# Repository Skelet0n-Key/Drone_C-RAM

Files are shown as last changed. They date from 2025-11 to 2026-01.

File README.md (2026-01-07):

# Project Overview

**Introduction**

Inspired by C-RAM/CIWS systems, an embedded systems semester-long team project was built. This ML vision air defense turret prototype is intended to combat small drones at close range, as a last line of defense. The system features dual TB6600s driving yaw and pitch stepper motors to their thermal limits. 3D printed and belt drive hardware allows for independent gear reduction for each axis. A Raspberry Pi 5 with locally running ML image recognition (YOLOv8) handles detection and sends coordinates on the screen to an Arduino via UART. The Arduino calculates the x and y stepper motor movement, using timers to send the correct frequency and steps to lock onto targets. The use of Raspberry Pi (Linux) and Arduino (bare metal C++) allows for ease of use, flexible programming, and direct real time control. The turret design accepts any AR style air-soft gun via piccatinny rail.

<p align="center">
  <a href="https://youtu.be/CiCFE5r0B4Y" target="_blank">
    YouTube Video Thumbnail
  </a>
  <br>
  <a href="https://youtu.be/CiCFE5r0B4Y" target="_blank">
    Watch demo video on YouTube
  </a>
  <br><br>
  <a href="https://www.youtube.com/playlist?list=PLNzJUv3sgPipa0nPbpG0y632YNqH1CYb0" target="_blank">
    View the full playlist here
  </a>
</p>

**Project Capabilities**

- Powered via standard 120V corded 24V power supply or 18-24V drill batteries. System intended to run on 24V DC.
- X stepper motor wires and main power runs through a 6 wire gold plated slip joint in the base of the turret, allowing for unrestricted 360 degree rotation.
- The sony IMX500 ASIC can be loaded with various tensorflow and yolo image recognition models. Read more here: [(+)](https://www.raspberrypi.com/documentation/accessories/ai-camera.html)
- The turret can be set to detect, track, and fire on drones or people. Target prediction is an option for both person and drone modes. 
- Can be configured to automatically run when plugged in. 
- Effective range: 20-30 feet.
- Theoretical max turret rotation: 150 rpm. Realistically, rotation speed is limited by when motion blur in the camera prevents ML from detecting targets, or when target leaves the frame too quickly for the turret to accelerate.  

**Timeline**

- Working model with object detection (10/14/25)
- Finished printing and received all parts to build the project (10/20/25)
- Project assembled (10/22/25)
- Motor control working (10/29/25)
- PID controller implemented, motor control refined (11/2/25)
- Turret locking on people (11/5/25)
- AI trained on drones (12/4/25)
- First field tests (12/6/25)

**Testing and Results**
- Ssd_mobilenet_v2 general ML model delivering exceptional results when filtered to detect people only.
- Custom yolov8 model trained on generic publc dataset delivering mediocre results. Detection spotty, drops frames, slow. Better dataset needed.
- Turret holds acceptable accuracy and is fast with good ML model
- Hard stop switches too sensitive, vibration from firing causes them to trip, recalibrating turret mid firing.
- Initial field test, 2 confirmed hits on drone.
- Second tests, C-RAM tracking incredibly well running around it ~25ft away. Discovered that it will lock onto people's shadows if the silhouette is human enough.

# Challenges & Solutions

**Learning to interface with the raspberry pi AI cam with integrated IMX500 ASIC to run ML locally**

The Libcamera library for the pi AI cam has been renamed rpicam, Libcamera is no longer in use. Our python script utilizes picamera2 to run a mobilenetSSD model, and cv2 to draw center mass points for output bounding boxes.

**Developing a robust driver for dual TB6600s and NEMA 17 stepper motors**

Finding max PUL speeds for our motors to avoid overloading and skipping. Finding min PUL pulse timing for smooth motion with reasonable micro-stepping. Finding optimal torque curves to avoid belt skipping and jitter. Method for finding these limits was trial and error, changing pusle speed in software and testing movements for hours. We settled on driving the TB6600s with arduino to supply the required 5v input signals and avoid Linux operating system real time control issues. By offloading stepper control to a bare metal micro controller we achieved smooth and precise control.

**Designing a printable frame, utilizing common and widely available hardware. (shafts, bearings, belts, etc...)**

We chose to use standard 3d printer parts for most of the hardware on the frame for accessibility and standardization. There are a couple random odds and ends like a 4" turntable bearing and a 6 wire gold contact slip joint for 360 degree rotation.

**Accurately calculating target lead**

The target lead is based off of the target's speed across the feed. This creates problems when the camera is on the turret, which is rotating. A target may be stationary, but the movement of the camera will cause it to think that the target is moving. It will calculate a lead and oscillate over the stationary target. We considered mounting the camera on the baseplate rather than move with the turret, but this creates more problems than it solves. The turret doesn't know its exact orientation, and a setup like this would need to. The mounted camera also allows for this feedback loop. Were it on the baseplate, the turret would constantly get misaligned and miss its target. Our best solution was to dampen the sent coordinates. This minimized oscillation and conveniently also helped the target leading algorithm to be more smooth.

**Implementing PID controller in C++ for smooth turret rotation**

The actual controller implementation is more of a PD controller. That is - the turret is rotated on its proportional and derivative components, or how far away the target is relative to center, and how fast the turret is approaching its target.

**Using a MOSFET to pull the trigger**

We thought that it would be nice to digitally pull the trigger. A MOSFET was the perfect addition. We ended up going with the N-channel IRLB8721 MOSFETs. After wiring it all up to the battery at drove the firing mechanism, the MOSFET started to smoke and melt the jumper wires. The battery GND and Arduino GND were connected, the specifications for the transistor weren't being exceeded... Due to an impending project deadline, we attached another stepper motor to the turret to pull the trigger. This comes with its own issues. We couldn't pull the power if the trigger was still held down, the Arduino needed to tell it to back off. Silver lining though, putting the battery on the outside of the stock balanced the turret a bit more.

**Turret pitching too violently on drone model**

Unfortunately, this was a result of an imperfect yolov8 model. Especially indoors, the model had a hard time keeping track of the drone. The turret updates its stepper-controlling timers everytime a coordinate is received from the RPI5. It has a timeout function to stop if it hasn't received a coordinate for a (long) time. Because the drone model was constantly timing out, it was over-rotating and then overcorrecting when it got a detection again. We patched this by lowering the timeout time. This actually made it timeout more, but stopped the turret from over-rotating. It makes the motion for drone tracking much more choppy. A permanent solution would be to get a more continuous output of coordinates with a better AI model, or to re-write the entire controller logic on the Arduino to handle less continuous coordinates better.

**Turret jerking on drone model**

This was an interesting issue. Prior to the updated stepper motor control code as it is now, the code used to have separated direction and speed control functions. This was an attempt to make portable, abstract, and modular code. What it ended up doing on less reliable models was jerking when switching directions. So if the drone was on the right side of the screen, it would accelerate right until the target moved, blinked and appeared on the left side of the screen. The speed controller was only aware of speed and distance to target, so the direction would switch instantaneously, while the frequency sent to the stepper motors stayed relatively the same. This wasn't an issue with a better model like tracking people. The detections didn't "blink" across the screen, there were continuous coordinates sent to the Arduino. The solution: unify the direction and frequency control functions. That way, if the turret is rotating clockwise but needs to rotate counter-clockwise, it decelerates to zero before switching directions.

**Turret re-calibrating when firing**

Earlier, we added buttons on the yolk that would be physically switched when the turret pitched too far up or down. The buttons would trigger an interrupt and the turret would "recover" or "re-calibrate." This recalibration was blocking, so perhaps it was for the best that we had issues here: for some reason, when the turret was firing this interrupt was triggering, despite neither button being pressed. We theorize that the vibration of the turret was somehow making the code go into that logic. Maybe the vibration was producing a signal on a victim line from some other aggressor line. We ended up doing away with the re-calibration logic.

# Hardware Components

* (5) 5mm x 250mm 304 Stainless Steel Solid Round Rod [(+)](https://www.amazon.com/dp/B082ZNJR7D?ref=ppx_yo2ov_dt_b_fed_asin_title&th=1)
* (12) Set Screw Collars [(+)](https://www.amazon.com/dp/B0F9P5CNSL?ref=ppx_yo2ov_dt_b_fed_asin_title&th=1)
* (15) Ball Bearings 5mm Bore 16mm OD [(+)](https://www.amazon.com/dp/B0CJFSBRTJ?ref=ppx_yo2ov_dt_b_fed_asin_title&th=1)
* (4) Flange Coupling Connector [(+)](https://www.amazon.com/dp/B0DN6P9B36?ref=ppx_yo2ov_dt_b_fed_asin_title&th=1)
* (2) Timing Pulley Set [(+)](https://www.amazon.com/dp/B09TKZS2QB?ref=ppx_yo2ov_dt_b_fed_asin_title&th=1)
* Turntable Bearing [(+)](https://www.amazon.com/dp/B08CSMYXFV?ref=ppx_yo2ov_dt_b_fed_asin_title&th=1)
* Raspberry Pi AI camera [(+)](https://www.adafruit.com/product/6009?srsltid=AfmBOoqx1-qlwzmA9ndyD2iXr5zASwpQUE9RnnWQQf-xEFGbjSt2rt4W)
* Stepper motor cables [(+)](https://www.amazon.com/dp/B07PZWXBFB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)
* Power supply [(+)](https://www.amazon.com/dp/B0CGHSTDYM?ref_=cm_sw_r_cp_ud_ct_X4HZC6Q636RNBEGBQEZB_1&th=1)
* Jumper cables [(+)](https://www.amazon.com/dp/B0CGHSTDYM?ref_=cm_sw_r_cp_ud_ct_X4HZC6Q636RNBEGBQEZB_1&th=1)
* Raspberry Pi 5 8GB [(+)](https://www.amazon.com/dp/B0CK2FCG1K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)
* (2) TB6600 stepper motor drivers [(+)](https://www.amazon.com/dp/B0BZYX7Z4Z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)
* Full automatic arisoft gun (some prints made specific to our model [(+)](https://www.amazon.com/dp/B07XJ9K5KT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))
* Slip joint [(+)](https://www.amazon.com/dp/B07XJ9K5KT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)
* Arduino Uno [(+)](https://www.amazon.com/Arduino-A000066-ARDUINO-UNO-R3/dp/B008GRTSV6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)
* 12V/24V to 5V Power Converter [(+)](https://www.amazon.com/dp/B0CJV6WV35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)

# Software Dependencies

Raspberry PI:

```bash
    sudo apt install imx500-all 
    sudo apt install python3-picamera2 --no-install-recommends
```

# Implementation

## Wiring Diagram
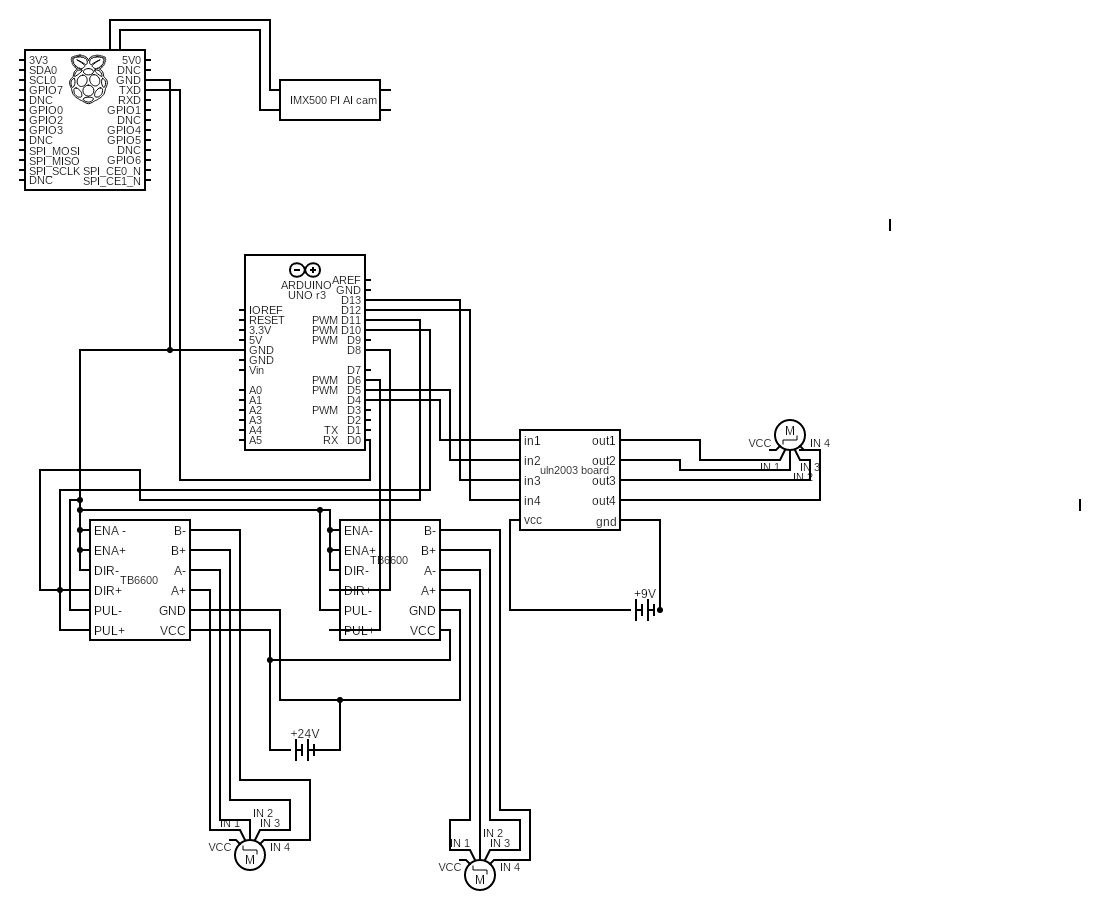
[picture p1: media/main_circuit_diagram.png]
wiring diagram


## CAD Files

We used a total of (seven) 3D printed parts on this project. You can find them here: [(+)](https://github.com/Skelet0n-Key/Drone_C-RAM/tree/main/CAD_files)

# Helpful Resources
- Raspberry PI AI Camera Guide [(+)](https://www.raspberrypi.com/documentation/accessories/ai-camera.html)
- Raspberry Pi AI Camera IMX500 Converter User Manual [(+)](https://developer.aitrios.sony-semicon.com/en/docs/raspberry-pi-ai-camera/imx500-converter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)
- Post-Training Quantization in PyTorch using the Model Compression Toolkit [(+)](https://github.com/SonySemiconductorSolutions/mct-model-optimization/blob/main/tutorials/notebooks/mct_features_notebooks/pytorch/example_pytorch_post_training_quant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)
- Export a Quantized Pytorch Model With the Model Compression Toolkit [(+)](https://github.com/SonySemiconductorSolutions/mct-model-optimization/blob/main/tutorials/notebooks/mct_features_notebooks/pytorch/example_pytorch_export.ipynb)
- MCT Features [(+)](https://github.com/SonySemiconductorSolutions/mct-model-optimization/tree/main/tutorials/notebooks/mct_features_notebooks)

# Acknowledgements
- We used an example from picamera2 [(+)](https://github.com/raspberrypi/picamera2/blob/3b2889e2c3eb1f05b5bb16d08be98b9f5355748f/examples/imx500/imx500_object_detection_demo.py) as the scaffolding for our ML_control [(+)](https://github.com/Skelet0n-Key/Drone_C-RAM/tree/main/ML_control) programs.

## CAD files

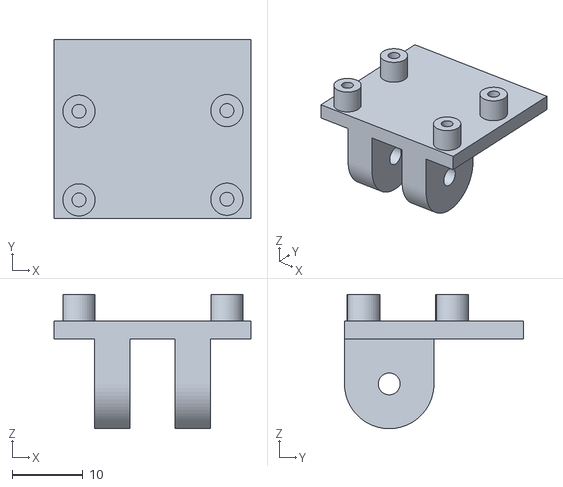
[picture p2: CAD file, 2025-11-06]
CAD_files/pi cam mount v2.stl
27.9 x 25.4 x 19.0

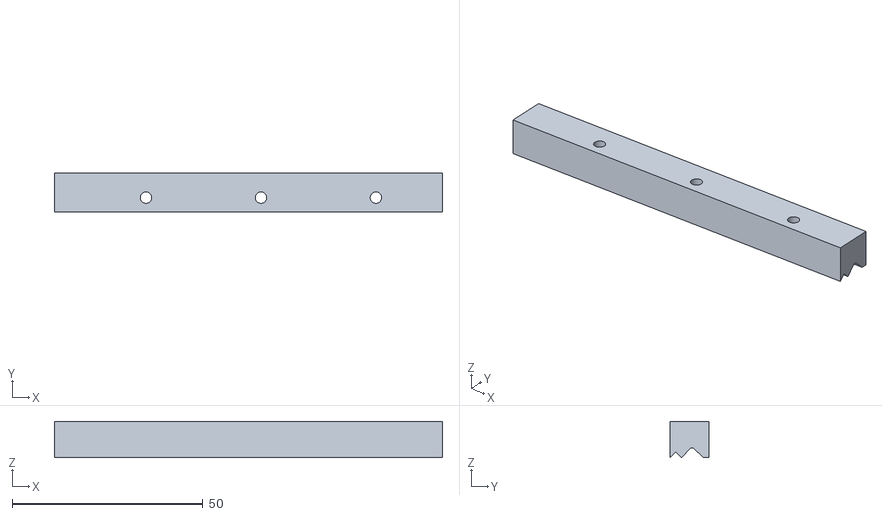
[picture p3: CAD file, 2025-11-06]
CAD_files/pic rail for gun mount v3.stl
101.6 x 10.2 x 9.48

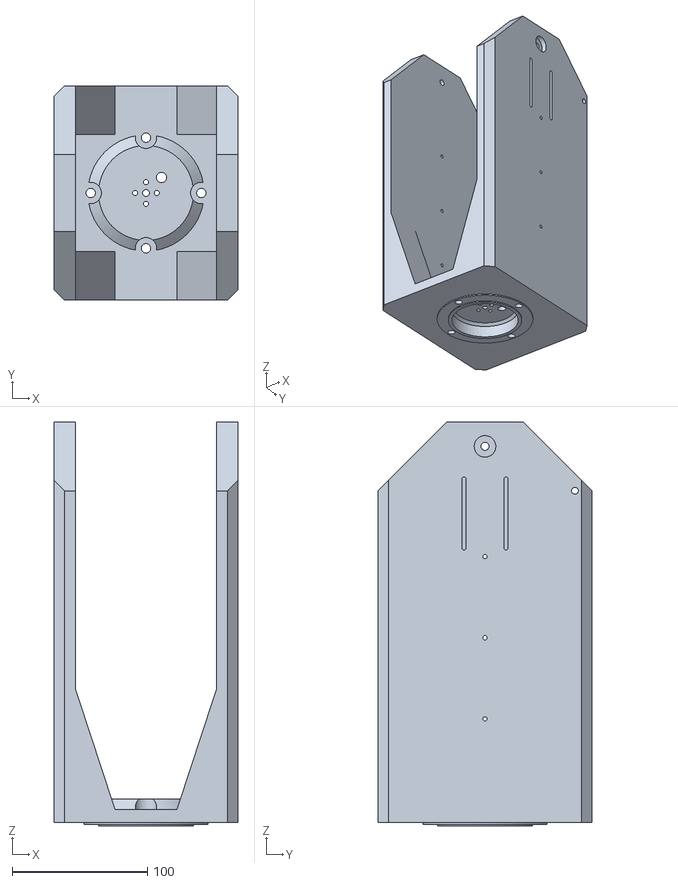
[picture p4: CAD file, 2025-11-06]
CAD_files/turret yoke v13.stl
135.9 x 158.1 x 298.5

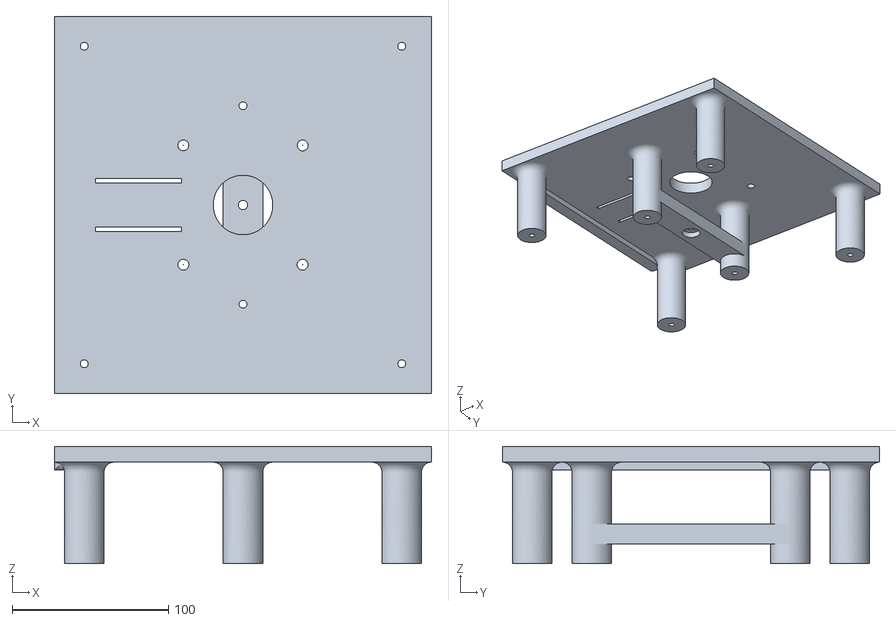
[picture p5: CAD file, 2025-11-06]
CAD_files/turret_baseplate_final v7.stl
241.3 x 241.3 x 75.2

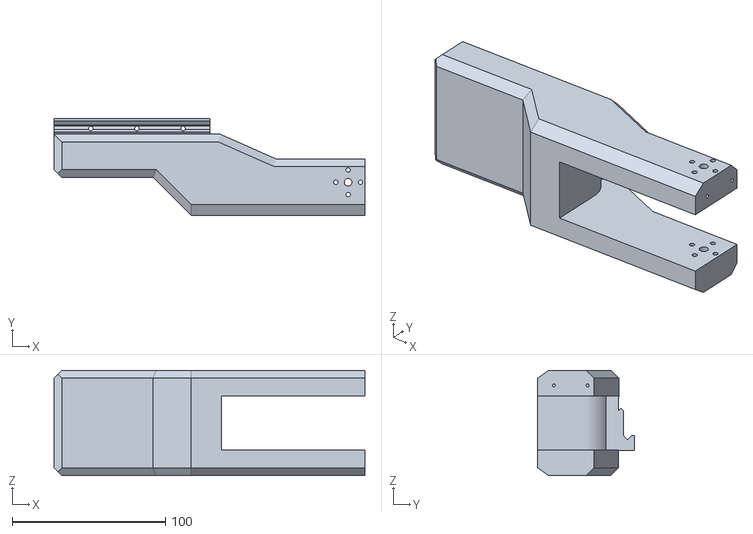
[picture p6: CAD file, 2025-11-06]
CAD_files/gun mount v7.stl
202.8 x 63.1 x 68.6

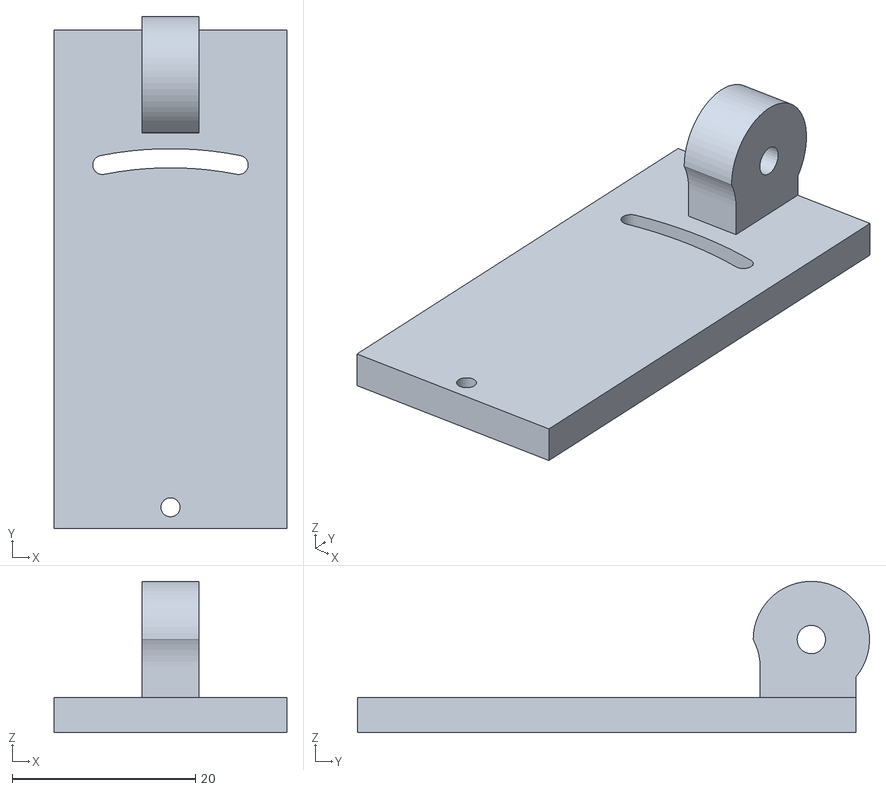
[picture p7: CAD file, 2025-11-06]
CAD_files/picam mount base v3.stl
25.4 x 55.9 x 16.5

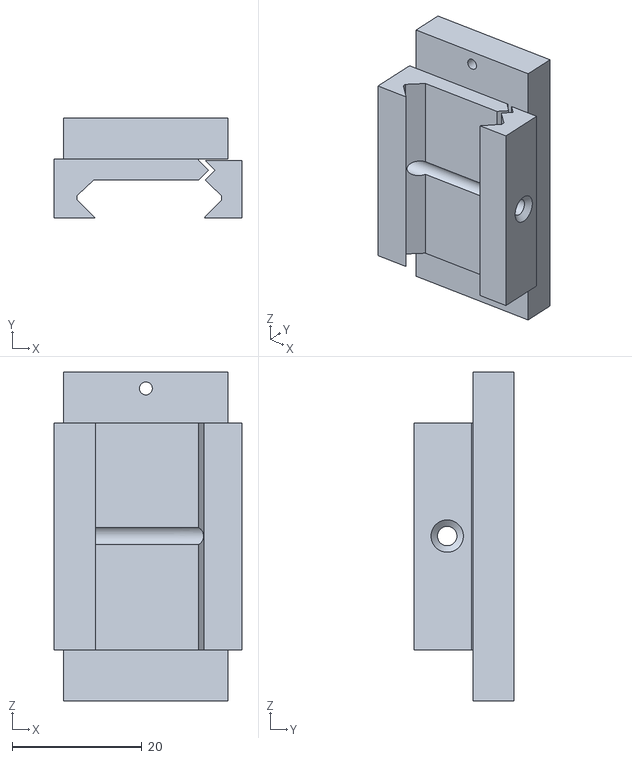
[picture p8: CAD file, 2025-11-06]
CAD_files/picamRailbase v3.stl
29.0 x 15.5 x 50.8

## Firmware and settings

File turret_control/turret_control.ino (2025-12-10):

/*
 Y tb6600 setting 4 microstep (on off off)
 X tb6600 setting 2b microstep(off on on)
 both amp setting 2.5 (off on on)
*/

#include <Arduino.h>

String coords = "";
int x = 0;
int y = 0;
int centerX = 320;
int centerY = 240;
int xFreq = 100;
int yFreq = 100;

int xPulsePin = 6;   // Timer0 OCR0A
int xDirPin = 8;
int yPulsePin = 11;  // Timer2 OCR2A
int yDirPin = 10;

// y-limit switches
const int Y_DOWN_LIMIT_PIN = 2;
const int Y_UP_LIMIT_PIN = 3;

volatile bool yLimitLock = false;
volatile bool yUpLimit = false;
volatile bool yDownLimit = false;
volatile bool yRecover = false;
volatile bool scan = false;

// ULN2003 stepper pins
const int STEP_IN1 = 4;
const int STEP_IN2 = 5;
const int STEP_IN3 = 12;
const int STEP_IN4 = 13;

int pinlist[] = {4, 5, 12, 13};

const int STEPS_PER_REV = 2048;
const int STEPS_PER_EIGHTH = STEPS_PER_REV / 2;

// Half-step sequence for trigger stepper
const int sequence[8][4] = {
  {1,0,0,0},
  {1,1,0,0},
  {0,1,0,0},
  {0,1,1,0},
  {0,0,1,0},
  {0,0,1,1},
  {0,0,0,1},
  {1,0,0,1}
};

// Stepper state
struct StepperState {
  int currentStep = 0;
  int stepsRemaining = 0;
  int direction = 1;
  unsigned long lastStepTime = 0;
  int stepDelay = 1; // ms
  bool active = false;
  bool stateFired = false; // has fire been triggered
} stepper;


// Timeout vars
volatile unsigned long timer1_millis = 0;
unsigned long millis_without_coords = 0;

// Turret behavior params
const double X_CURVE_COEFFICIENT = 2;
const int X_FREQ_MAX = 2000;
const int X_FREQ_MIN = 31;
const int X_ACCEL_LIMIT = 70;
const double Y_CURVE_COEFFICIENT = 4;
const int Y_FREQ_MAX = 2000;
const int Y_FREQ_MIN = 31;
const int Y_ACCEL_LIMIT = 50;

const int X_DEADZONE = 15;  // true deadzone is times two
const int Y_DEADZONE = 15;

const int X_FIRE_DEADZONE = 30;
const int Y_FIRE_DEADZONE = 30;

// Function prototypes for turret control
void stopTimer0();
void startTimer0();
void stopTimer2();
void startTimer2();
void setxFreq(int xFreq);
void setyFreq(int yFreq);
int xfrequency_calculator(int coord, int curr_freq, int center);
int yfrequency_calculator(int coord, int curr_freq, int center);
void set_dir(char axis, int center, int coord);

// Stepper functions
void updateStepper();
void driveStepper(bool fire);
void releaseCoils();

void setup() {
  // Timer0 - prescaler 1024, 1kHz output on Pin 6 (X-axis)
  TCCR0A = (1 << COM0A0) | (1 << WGM01);  // Toggle mode, CTC mode
  TCCR0B = (1 << CS02) | (1 << CS00);     // Prescaler 1024
  OCR0A = (uint8_t)((F_CPU / (2UL * 1024UL * 1000UL)) - 1);

  // Timer1 setup for 1ms interrupts
  TCCR1A = 0;  // Normal mode
  TCCR1B = (1 << WGM12) | (1 << CS11) | (1 << CS10);  // CTC mode, prescaler 64
  TCNT1 = 0;
  OCR1A = 249;  // 16MHz / 64 / 250 = 1000 Hz (1ms)
  TIMSK1 |= (1 << OCIE1A);  // Enable compare interrupt
  sei();  // Enable global interrupts
  
  // Timer2 - prescaler 1024, 1kHz output on Pin 11 (Y-axis)
  TCCR2A = (1 << COM2A0) | (1 << WGM21);  // Toggle mode, CTC mode
  TCCR2B = (1 << CS22) | (1 << CS21) | (1 << CS20);  // Prescaler 1024
  OCR2A = (uint8_t)((F_CPU / (2UL * 1024UL * 1000UL)) - 1);
  
  pinMode(xPulsePin, OUTPUT);
  pinMode(xDirPin, OUTPUT);
  pinMode(yPulsePin, OUTPUT);
  pinMode(yDirPin, OUTPUT);

  pinMode(4, OUTPUT);
  pinMode(5, OUTPUT);
  pinMode(12, OUTPUT);
  pinMode(13, OUTPUT);

  pinMode(Y_UP_LIMIT_PIN, INPUT_PULLUP);
  pinMode(Y_DOWN_LIMIT_PIN, INPUT_PULLUP);

  attachInterrupt(digitalPinToInterrupt(Y_UP_LIMIT_PIN), yUpLimitISR, FALLING);
  attachInterrupt(digitalPinToInterrupt(Y_DOWN_LIMIT_PIN), yDownLimitISR, FALLING);
  
  Serial.begin(115200);
  
  stopTimer0();  // Changed from stopTimer1()
  stopTimer2();
}

ISR(TIMER1_COMPA_vect) {
  timer1_millis++;
}

unsigned long timer1_millis_get() {
  unsigned long m;
  noInterrupts();
  m = timer1_millis;
  interrupts();
  return m;
}

void yUpLimitISR() {
  yRecover = true;
  yUpLimit = true;
  yDownLimit = false;
}

void yDownLimitISR() {
  yRecover = true;
  yUpLimit = false;
  yDownLimit = true;
}



// ===============================================================
// ===============================================================


void loop() {
  // Recover logic
  // if (yRecover) {
  //   stopTimer0();
  //   stopTimer2();

  //   if (yUpLimit) {
  //     digitalWrite(yDirPin, LOW);
  //     setyFreq(150);
  //     startTimer2();
  //   }
  //   if (yDownLimit) {
  //     digitalWrite(yDirPin, HIGH);
  //     setyFreq(250);
  //     startTimer2();
  //   }

  //   unsigned long yRecoverMillis = timer1_millis_get();
  //   while (timer1_millis_get() - yRecoverMillis <= 2000) {
  //     true;
  //   }
  //   stopTimer2();
  //   yRecover = false;
  //   yUpLimit = false;
  //   yDownLimit = false;
  //   scan = true;
  // }

  unsigned long curr_millis = timer1_millis_get();

  // Timeout logic
  if ((curr_millis - millis_without_coords >= 600) && (scan == false)) {
    stopTimer0();
    stopTimer2();
    // digitalWrite(yDirPin, LOW);
    // setyFreq(150);
    // startTimer2();
  }

  // if (scan == true) {
  //   digitalWrite(xDirPin, HIGH);
  //   setxFreq(50);
  //   startTimer0();
  // }

  // Serial input parsing
  while (Serial.available() > 0) {
    char c = Serial.read();
    if (c == '\n') {
      int commaIndex = coords.indexOf(',');
      x = coords.substring(0, commaIndex).toInt();
      y = coords.substring(commaIndex + 1).toInt();

      xFreq = x_controller(x, centerX, xFreq);
      yFreq = y_controller(y, centerY, yFreq);

      setxFreq(xFreq);
      setyFreq(yFreq);

      coords = "";
      millis_without_coords = curr_millis;
      scan = false;
    } else coords += c;
  }
  
  bool xDead = abs(x - centerX) <= X_FIRE_DEADZONE;
  bool yDead = abs(y - centerY) <= Y_FIRE_DEADZONE;

  if (xDead && yDead) {
    // Fire when in dead zone
    driveStepper(true);
  } else {
    // Reverse to original position when leaving dead zone
    driveStepper(false);
  }

  // Non-blocking stepper update
  updateStepper();

}

// timer and frequency functions
void stopTimer0() {
  TCCR0A &= ~(1 << COM0A0);  // Changed from TCCR1A and COM1A0
  digitalWrite(xPulsePin, LOW);
}

void startTimer0() {
  TCCR0A |= (1 << COM0A0);
}

void stopTimer2() {
  TCCR2A &= ~(1 << COM2A0);
  digitalWrite(yPulsePin, LOW);
}

void startTimer2() {
  TCCR2A |= (1 << COM2A0);
}

void setxFreq(int xFreq) {
  OCR0A = (F_CPU / (2UL * 1024UL * (unsigned long)xFreq)) - 1;  // Changed OCR1A to OCR0A, and 256 to 1024
}

void setyFreq(int yFreq) {
  OCR2A = (F_CPU / (2UL * 1024UL * (unsigned long)yFreq)) - 1;
}

int x_controller(int coord, int center, int curr_freq) {
  int distance = coord - center;
  int target_freq = constrain(abs(distance) * X_CURVE_COEFFICIENT, X_FREQ_MIN, X_FREQ_MAX);

 // ====== TRAVELLING POSITIVE ======

  if (digitalRead(xDirPin) == LOW) {
    if (distance > X_DEADZONE) {  // normal behavior: accel/decel based on target freq, we're already travelling in the right direction
      if (curr_freq < target_freq) {
        startTimer0();
        digitalWrite(xDirPin, LOW);
        return constrain(curr_freq + X_ACCEL_LIMIT, X_FREQ_MIN, X_FREQ_MAX);
      } else if (curr_freq > target_freq) {
        startTimer0();
        digitalWrite(xDirPin, LOW);
        return constrain(curr_freq - X_ACCEL_LIMIT, X_FREQ_MIN, X_FREQ_MAX);
      }
      startTimer0();
      digitalWrite(xDirPin, LOW);
      return curr_freq;
    } else if (distance < -1*X_DEADZONE) {  // dir is positive and we are travelling in the wrong direction; turn around
      if (curr_freq == X_FREQ_MIN) {  // end case: we've decelerated as much as we can, now we can turn around
        digitalWrite(xDirPin, HIGH);
        startTimer0();
        return curr_freq;
      }
      startTimer0();
      digitalWrite(xDirPin, LOW);
      return constrain(curr_freq - X_ACCEL_LIMIT, X_FREQ_MIN, X_FREQ_MAX);  // decel
    } else {  // We're in the deadzone: halt
      stopTimer0();
      return X_FREQ_MIN;
    }

   // ====== TRAVELLING NEGATIVE ======

  } else {
    if (distance > X_DEADZONE) {  // we need to turn around if this is true
      if (curr_freq == X_FREQ_MIN) {
        startTimer0();
        digitalWrite(xDirPin, LOW);
        return curr_freq;
      }
      startTimer0();
      digitalWrite(xDirPin, HIGH);
      return constrain(curr_freq - X_ACCEL_LIMIT, X_FREQ_MIN, X_FREQ_MAX);  // decel
    } else if (distance < -1*X_DEADZONE) {  // normal behavior, accel/decel based on target frequency
      if (curr_freq < target_freq) {
        startTimer0();
        digitalWrite(xDirPin, HIGH);
        return constrain(curr_freq + X_ACCEL_LIMIT, X_FREQ_MIN, X_FREQ_MAX);
      } else if (curr_freq > target_freq) {
        startTimer0();
        digitalWrite(xDirPin, HIGH);
        return constrain(curr_freq - X_ACCEL_LIMIT, X_FREQ_MIN, X_FREQ_MAX);
      }
      startTimer0();
      digitalWrite(xDirPin, HIGH);
      return curr_freq;
    } else {  // in deadzone, halt
      stopTimer0();
      return X_FREQ_MIN;
    } 
  }
}

int y_controller(int coord, int center, int curr_freq) {
  int distance = coord - center;
  int target_freq = constrain(abs(distance) * Y_CURVE_COEFFICIENT, Y_FREQ_MIN, Y_FREQ_MAX);

 // ====== TRAVELLING POSITIVE ======

  if (digitalRead(yDirPin) == LOW) {
    if (distance > Y_DEADZONE) {  // normal behavior: accel/decel based on target freq, we're already travelling in the right direction
      if (curr_freq < target_freq) {
        startTimer2();
        digitalWrite(yDirPin, LOW);
        return constrain(curr_freq + Y_ACCEL_LIMIT, Y_FREQ_MIN, Y_FREQ_MAX);
      } else if (curr_freq > target_freq) {
        startTimer2();
        digitalWrite(yDirPin, LOW);
        return constrain(curr_freq - Y_ACCEL_LIMIT, Y_FREQ_MIN, Y_FREQ_MAX);
      }
      startTimer2();
      digitalWrite(yDirPin, LOW);
      return curr_freq;
    } else if (distance < -1*Y_DEADZONE) {  // dir is positive and we are travelling in the wrong direction; turn around
      if (curr_freq == Y_FREQ_MIN) {  // end case: we've decelerated as much as we can, now we can turn around
        digitalWrite(yDirPin, HIGH);
        startTimer2();
        return curr_freq;
      }
      startTimer2();
      digitalWrite(yDirPin, LOW);
      return constrain(curr_freq - Y_ACCEL_LIMIT, Y_FREQ_MIN, Y_FREQ_MAX);  // decel
    } else {  // We're in the deadzone: halt
      stopTimer2();
      return Y_FREQ_MIN;
    }

   // ====== TRAVELLING NEGATIVE ======

  } else {
    if (distance > Y_DEADZONE) {  // we need to turn around if this is true
      if (curr_freq == Y_FREQ_MIN) {
        startTimer2();
        digitalWrite(yDirPin, LOW);
        return curr_freq;
      }
      startTimer2();
      digitalWrite(yDirPin, HIGH);
      return constrain(curr_freq - Y_ACCEL_LIMIT, Y_FREQ_MIN, Y_FREQ_MAX);  // decel
    } else if (distance < -1*Y_DEADZONE) {  // normal behavior, accel/decel based on target frequency
      if (curr_freq < target_freq) {
        startTimer2();
        digitalWrite(yDirPin, HIGH);
        return constrain(curr_freq + Y_ACCEL_LIMIT, Y_FREQ_MIN, Y_FREQ_MAX);
      } else if (curr_freq > target_freq) {
        startTimer2();
        digitalWrite(yDirPin, HIGH);
        return constrain(curr_freq - Y_ACCEL_LIMIT, Y_FREQ_MIN, Y_FREQ_MAX);
      }
      startTimer2();
      digitalWrite(yDirPin, HIGH);
      return curr_freq;
    } else {  // in deadzone, halt
      stopTimer2();
      return Y_FREQ_MIN;
    } 
  }
}

// Trigger stepper functions
void updateStepper() {
  if (!stepper.active) return;

  unsigned long now = timer1_millis_get();
  if (now - stepper.lastStepTime >= stepper.stepDelay) {
    stepper.currentStep = (stepper.currentStep + stepper.direction + 8) % 8;
    for (int i = 0; i < 4; i++) {
      digitalWrite(pinlist[i], sequence[stepper.currentStep][i]);
    }
    stepper.lastStepTime = now;
    stepper.stepsRemaining--;

    if (stepper.stepsRemaining <= 0) {
      stepper.active = false;
      releaseCoils();
    }
  }
}

void driveStepper(bool fire) {
  if (fire && !stepper.stateFired && !stepper.active) {
    stepper.active = true;
    stepper.direction = 1;
    stepper.stepsRemaining = STEPS_PER_EIGHTH;
    stepper.stateFired = true;
  } else if (!fire && stepper.stateFired && !stepper.active) {
    stepper.active = true;
    stepper.direction = -1;
    stepper.stepsRemaining = STEPS_PER_EIGHTH;
    stepper.stateFired = false;
  }
}

void releaseCoils() {
  for (int i = STEP_IN1; i <= STEP_IN4; i++) digitalWrite(i, LOW);
}

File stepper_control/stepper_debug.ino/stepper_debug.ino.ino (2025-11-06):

const int step1out = 8;
const int dir1out  = 9;
const int step2out = 10;
const int dir2out  = 11;

const int stepsPerTest = 150; // total steps per move
const int startDelay = 10000;   // slowest delay (µs)
const int minDelay = 2000;     // fastest delay (µs)800 max
const int rampSteps = 15;    // how many steps to ramp up/down ~100 min

void setup() {
  pinMode(step1out, OUTPUT);
  pinMode(dir1out, OUTPUT);
  pinMode(step2out, OUTPUT);
  pinMode(dir2out, OUTPUT);

  // Initialize outputs
  digitalWrite(step1out, HIGH);
  digitalWrite(step2out, HIGH);
  digitalWrite(dir1out, HIGH);  // forward
  digitalWrite(dir2out, HIGH);

  delay(500);
}

void loop() {
  digitalWrite(dir1out, HIGH);
  digitalWrite(dir2out, HIGH);
  rampedMove(stepsPerTest);
  delay(1000);

  digitalWrite(dir1out, LOW);
  //digitalWrite(dir2out, LOW);
  rampedMove(stepsPerTest);
  delay(3000);
}

void rampedMove(int stepsTotal) {
  int delayTime = startDelay;
  int halfSteps = stepsTotal / 2;

  // --- ACCELERATION PHASE ---
  for (int i = 0; i < rampSteps; i++) {
    delayTime = map(i, 0, rampSteps, startDelay, minDelay);
    doStep(delayTime);
  }

  // --- CONSTANT SPEED PHASE ---
  for (int i = rampSteps; i < stepsTotal - rampSteps; i++) {
    doStep(minDelay);
  }

  // --- DECELERATION PHASE ---
  for (int i = 0; i < rampSteps; i++) {
    delayTime = map(i, 0, rampSteps, minDelay, startDelay);
    doStep(delayTime);
  }
}

void doStep(int delayTime) {
  digitalWrite(step1out, LOW);
  digitalWrite(step2out,LOW);
  delayMicroseconds(delayTime);
  digitalWrite(step1out, HIGH);
  digitalWrite(step2out, HIGH);
  delayMicroseconds(delayTime);
}

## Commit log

2025-11-05 first rev of pid test for controlling stepper motors
2025-11-05 updated pid test
2025-11-06 replaced old prediction function with cv2 kalman filter
2025-11-06 tuned kalman filter
2025-11-06 fix i think??
    [gun mount v7.stl, pi cam mount v2.stl, pic rail for gun mount v3.stl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]
2025-11-06 changed max speed on stepper program from 500 to 1000
2025-11-06 added ability to pull trigger on dead zone in stepper controller
2025-11-11 split the x and y frequency calculator to be tuned separately. Fixed an issue with the acceleration curve not capping properly
    [PID_test_fire.ino]
2025-11-13 tuned stepper control-accelerate based on distance
2025-11-19 changed timer1(16 bit) to timer 0 (8bit)
2025-11-20 changed timeout to run on home-grown millis function so it doesn't conflict with timer0
    [turret_control.ino]
2025-11-25 added back in the stepper motor functions for pulling the trigger
2025-12-02 added y limit buttons and a recovery routine
2025-12-03 possible fix to coordinate scaling issue
    [yoloDrone.py]
2025-12-03 swapped x and y bounding box directions.
    [yoloDrone.py]
2025-12-03 added hold frame function and decreased confidence threshold
2025-12-09 Add wiring diagram to README
2025-12-10 cleaned turret_control code on arduino
2025-12-10 renamed 'stepper_debug.ino' folder. .ino isn't a folder . _ .
